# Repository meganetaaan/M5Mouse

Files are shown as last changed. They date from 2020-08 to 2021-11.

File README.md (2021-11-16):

# M5Mouse

A micro mouse PCB module & Software for M5Stack.

## Documents

Assembly and proguramming instructions are documented in the blog series "ししかわのマウス研修（Sskw's micro mouse training）"

- [Japanese](https://rt-net.jp/mobility/archives/9589#toc2)
- [English (auto translate)](https://1-rt--net-jp.translate.goog/mobility/archives/9589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)

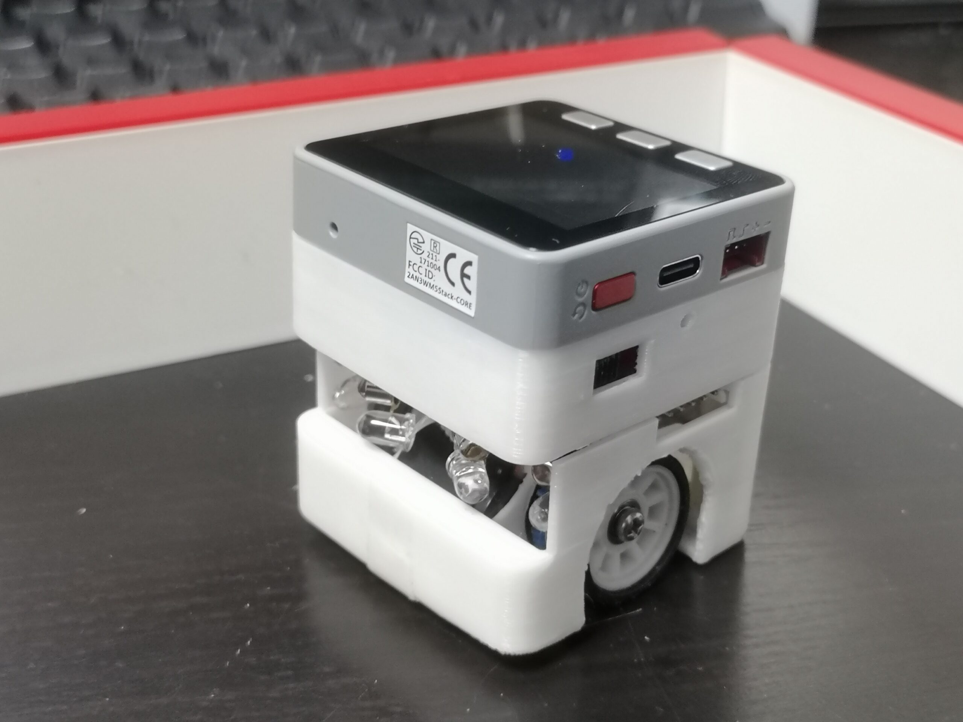
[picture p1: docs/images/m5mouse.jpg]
M5Mouse


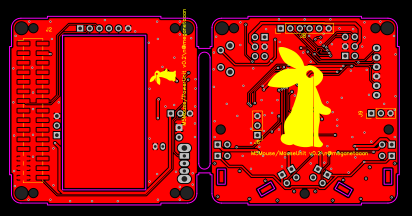
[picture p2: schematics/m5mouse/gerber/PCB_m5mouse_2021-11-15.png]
PCB


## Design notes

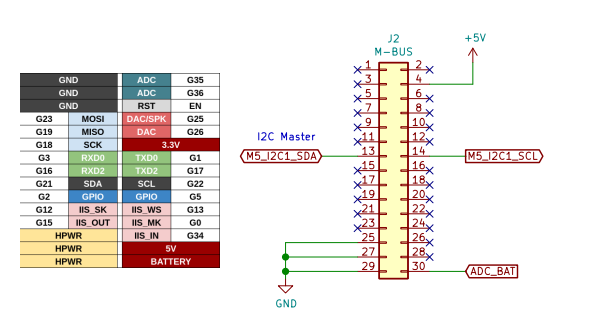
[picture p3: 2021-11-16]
schematics/m5mouse/gerber/M5mouse_pins.png

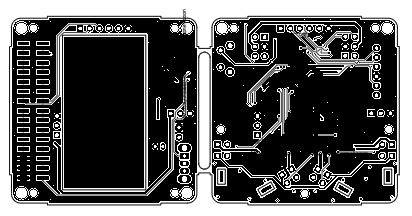
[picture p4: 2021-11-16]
schematics/m5mouse/gerber/PCB_m5mouse_schematic_2021-11-15.png

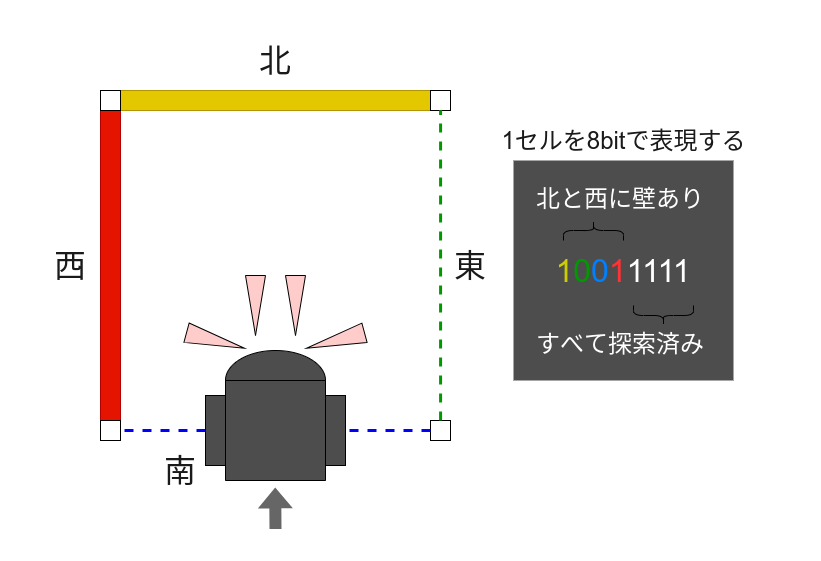
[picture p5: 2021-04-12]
design/cell.drawio.png

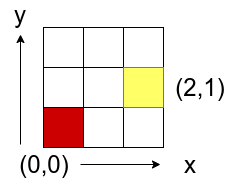
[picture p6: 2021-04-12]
design/maze.drawio.png

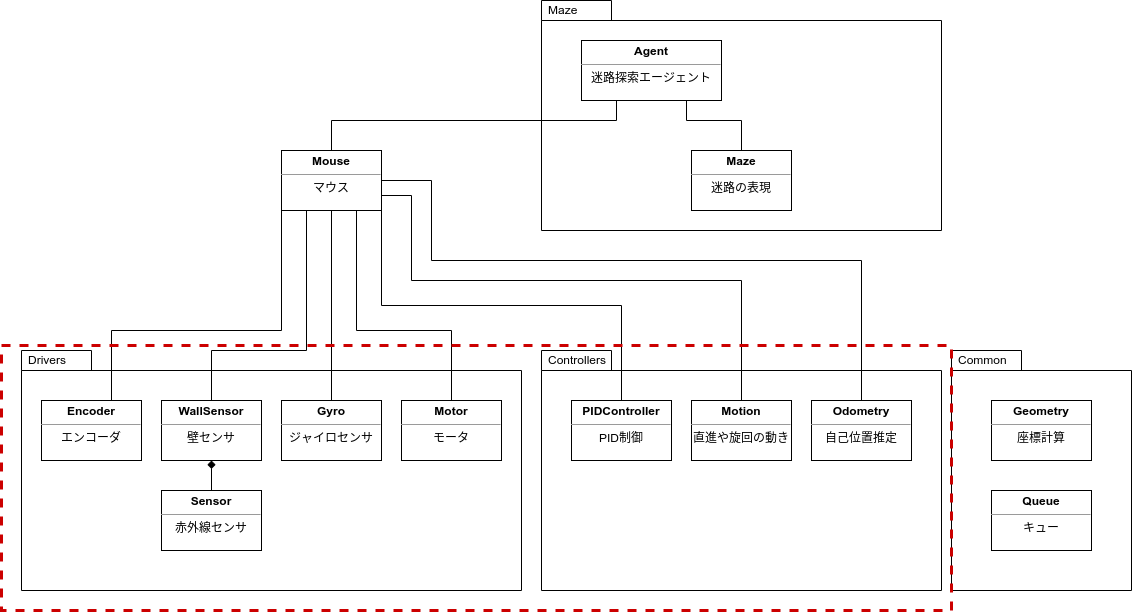
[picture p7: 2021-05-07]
design/class_diagram.drawio.png

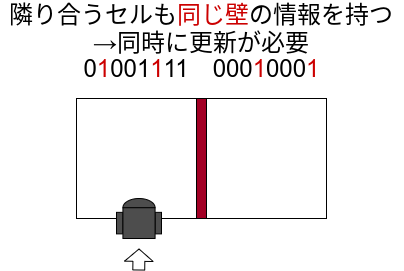
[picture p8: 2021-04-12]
design/neighbor_cells.drawio.png

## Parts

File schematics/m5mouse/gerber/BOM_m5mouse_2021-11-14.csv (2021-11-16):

ID | Name | Designator | Footprint | Quantity | Manufacturer Part | Manufacturer | Supplier | Supplier Part | Price
1 | 0.1u | C3,C4,C11,C12,C13,C14,C16,C20,C21,C22,C29,C30,C31 | C_0402_1005METRIC | 13
2 | 4.7u | C10 | C_0402_1005METRIC | 1
3 | 0.01u | C15 | C_0402_1005METRIC | 1
4 | 1u | C17,C28 | C_0402_1005METRIC | 2
5 | 10u | C18,C19,C25 | C_0402_1005METRIC | 3
6 | 2.2u | C23,C24 | C_0402_1005METRIC | 2
7 | 0.47u | C26 | C_0402_1005METRIC | 1
8 | LED 3.3V | D6,D7 | LED_0603_1608METRIC | 2
9 | LM3940IMP-3.3_NOPB | IC1 | LM3940IMP-3.3NOPB | 1
10 | Conn_02x03_Odd_Even | J4,J5 | PINHEADER_2X03_P2.54MM_VERTICAL | 2
11 | Conn_01x06 | J7 | PINSOCKET_1X06_P2.54MM_VERTICAL | 1
12 | 10u | L1 | L_1008_2520METRIC | 1
13 | BSS138 | Q1,Q3,Q5,Q7 | SOT-23 | 4
14 | 10k | R1,R6,R8,R10,R12,R14,R18 | R_0603_1608METRIC | 7
15 | 5.9k 1% | R2 | R_0603_1608METRIC | 1
16 | 1.07k 1% | R3 | R_0603_1608METRIC | 1
17 | 0 | R4 | R_0603_1608METRIC | 1
18 | 33 | R5 | R_0603_1608METRIC | 1
19 | 1k | R7,R9,R11,R13,R15,R16,R20 | R_0603_1608METRIC | 7
20 | 18k 1% | R17 | R_0603_1608METRIC | 1
21 | 10k 1% | R19 | R_0603_1608METRIC | 1
22 | TPS562200 | U1 | SOT-23-6 | 1
23 | STM32F405RGTx | U2 | LQFP-64_10X10MM_P0.5MM | 1
24 | DRV8835 | U3 | WSON-12-1EP_3X2MM_P0.5MM_EP1X2.65 | 1
25 | 8MHz | Y1 | CSTNE8M00G55Z000R0 | 1
26 | ICM-20648 | U4 | QFN-24-1EP_3X3MM_P0.4MM_EP1.75X1.6MM | 1
27 | SFH4550 | D2,D3,D4,D5 | THROUGHHOLE_1X02_P2.54_VERTICAL | 4
28 | ST-1KL3A | Q2,Q4,Q6,Q8 | THROUGHHOLE_1X02_P2.54_VERTICAL | 4
29 | 10u | C1,C2 | C_0603_1608METRIC | 2
30 | 22u | C5,C6,C7 | C_0805_2012METRIC | 3
31 | 33u | C27 | C_1206_3216METRIC | 1
32 | LED 5V | D1 | LED_D3.0MM_HORIZONTAL_O1.27MM_Z2.0MM | 1
33 | 0 | R21 | R_0603_1608METRIC_PAD1.05X0.95MM_HANDSOLDER | 1
34 | SWD | J3 | JST_EH_S6B-EH_1X06_P2.50MM_HORIZONTAL | 1
35 | 32.768kHz | Y2 | WMRAG32K76CS3C00R0 | 1
36 | 1p | C8,C9 | C_0201_0603METRIC | 2
37 | Ferrite_Bead | FB1 | R_0603_1608METRIC | 1
38 | SW_SPDT | SW1 | SW_CUK_OS102011MA1QN1_SPDT_ANGLED | 1
39 | SW_Push | SW2 | SW_TACTILE_SPST_ANGLED_PTS645VX39-2LFS | 1
40 | Conn_01x02 | J1 | JST_PH_S2B-PH-K_1X02_P2.00MM_HORIZONTAL | 1
41 | Conn_01x03 | J10,J11 | PINSOCKET_1X03_P2.54MM_VERTICAL | 2
42 | LOGO | G | RTMARK_7X7MM | 1
43 | LOGO | G | RT_MARK1_30X30 | 1
44 | MountingHole_2.2mm_M2 | MH10,MH6,MH7 | MOUNTINGHOLE_2.2MM_M2 | 3
45 | mountinghole_M2_M3 | MH8,MH5,MH2,MH3,MH4,MH1 | MOUNTINGHOLE_M2_M3 | 6
46 | M-BUS | J2 | PINHEADER_2X15_P2.54MM_VERTICAL_SMD | 1
47 | Conn_01x06 | J8 | PINHEADER_1X06_P2.54MM_VERTICAL | 1
48 | Conn_01x03 | J6,J9 | PINHEADER_1X03_P2.54MM_VERTICAL | 2

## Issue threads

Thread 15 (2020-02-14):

仮の外装作成

meganetaaan, 2020-02-14:
モータ周辺の外装を作成する。基板は無し。モータを取り付けて動かせればよい。

* [x] 情報収集
  * [x] Faulhaberなど使えそうな3Dモデルを入手する
  * [x] ギヤ・ホイールをFusion360で作る方法を知る
* [x] モータ周りの外装作成
* [x] テストプリント

meganetaaan, 2020-09-30:
作成済み
https://myhub.autodesk360.com/ue29f17411/g/shares/SH919a0QTf3c32634dcf1766a10e55d00c86

Closed 2020-11-20.

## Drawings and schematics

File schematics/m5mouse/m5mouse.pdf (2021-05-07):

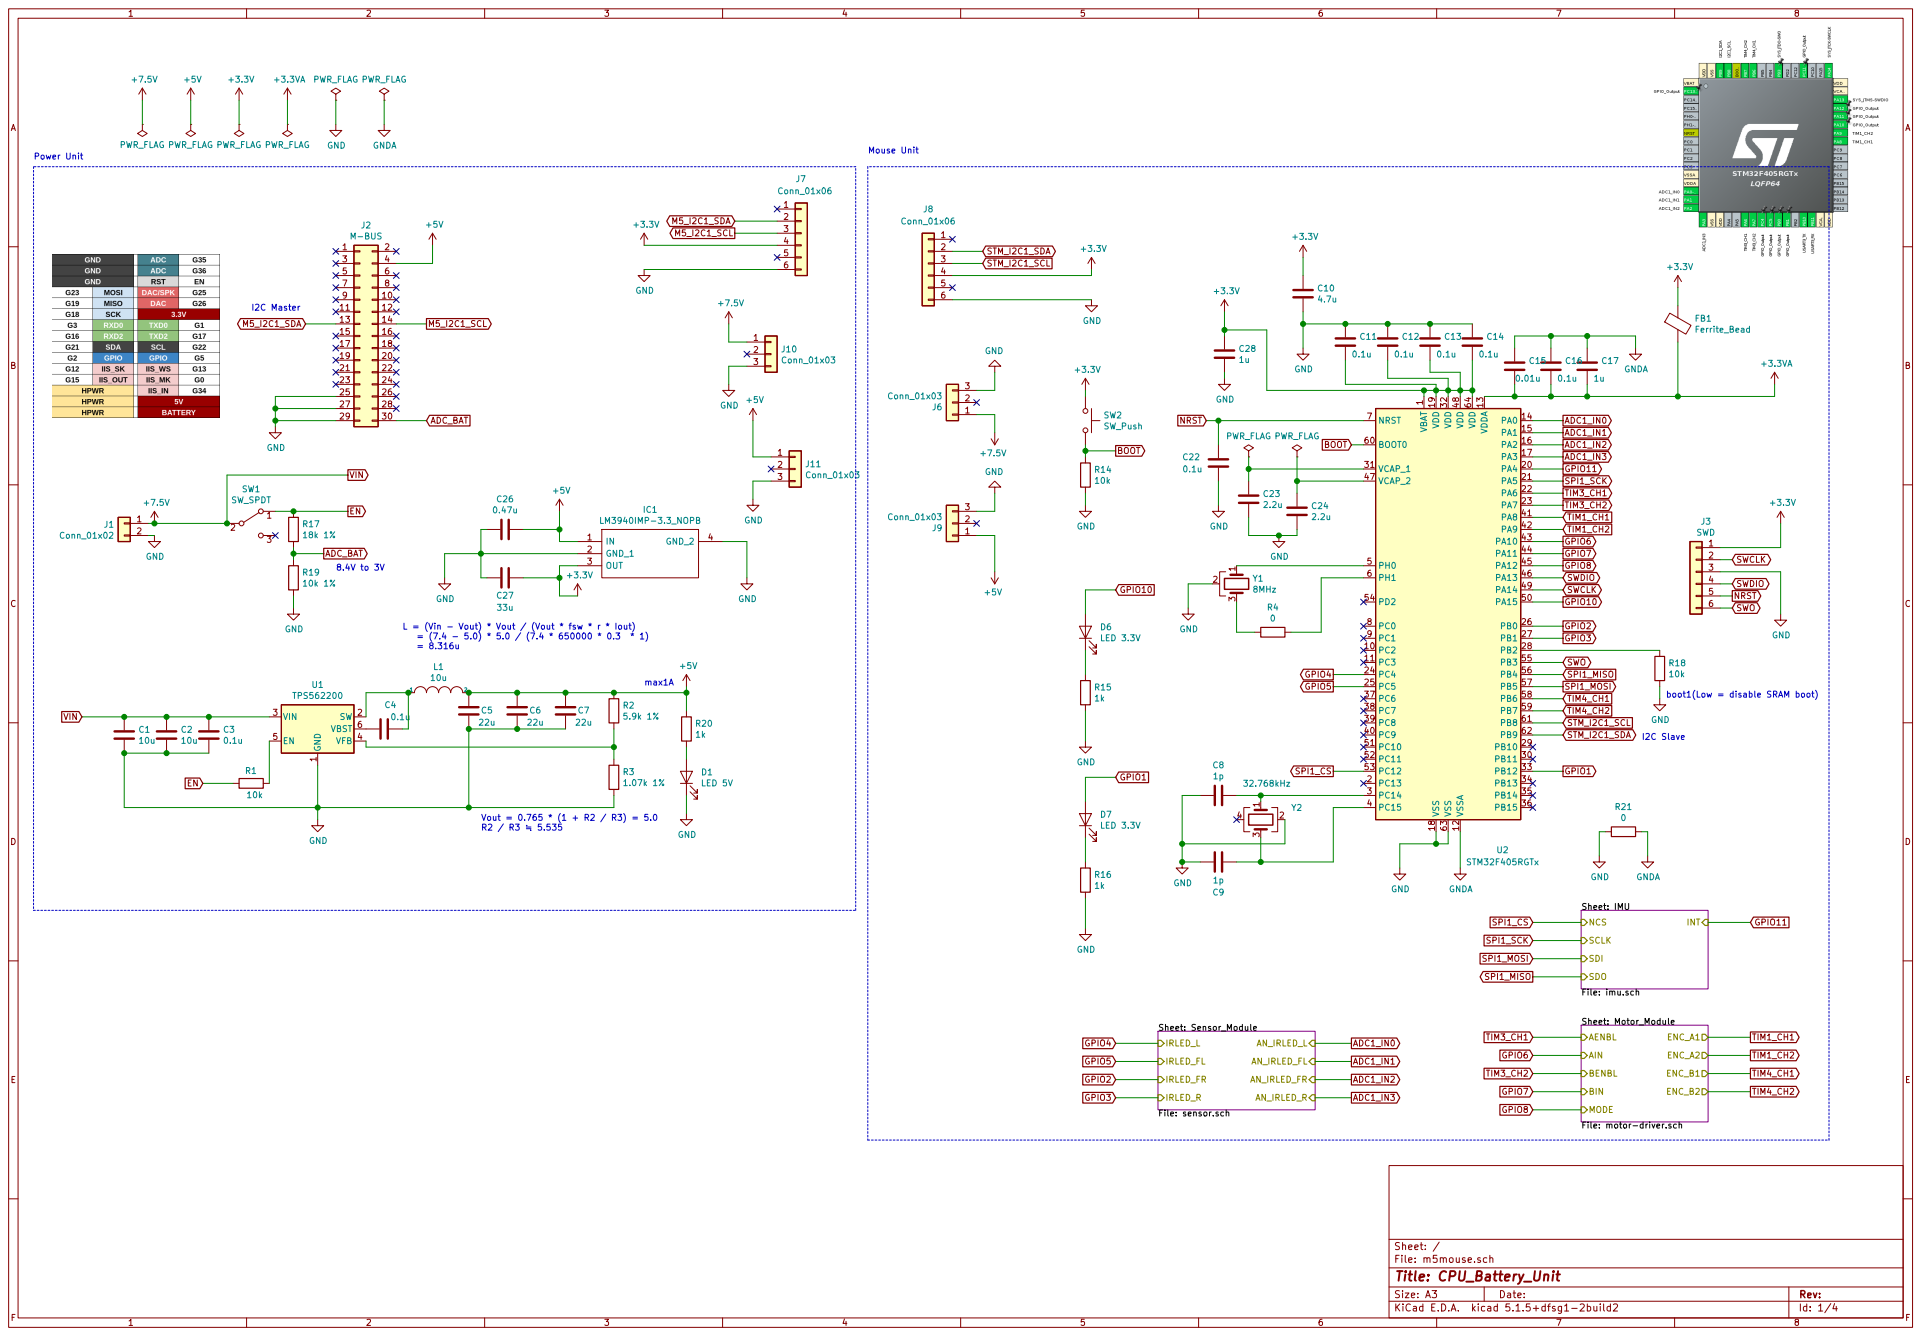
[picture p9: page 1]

1 VCAP_1 31 VCAP_2 47 VDD 19 VDD 32 VDD 48 VDD 64 VDDA 13 VSS 18 VSS 63 VSSA 12 U2 STM32F405RGTx GNDA GND
GPIO6 SPI1_MISO

L = (Vin - Vout) * Vout / (Vout * fsw * r * Iout)

1 SW 2 VIN 3 VFB 4 EN 5 VBST 6 U1 TPS562200

INT Sheet: Motor_Module File: motor-driver.sch AENBL AIN

File: imu.sch SDO

Id: 1/4 Title: CPU_Battery_Unit File: m5mouse.sch Sheet: / Sheet: Sensor_Module File: sensor.sch

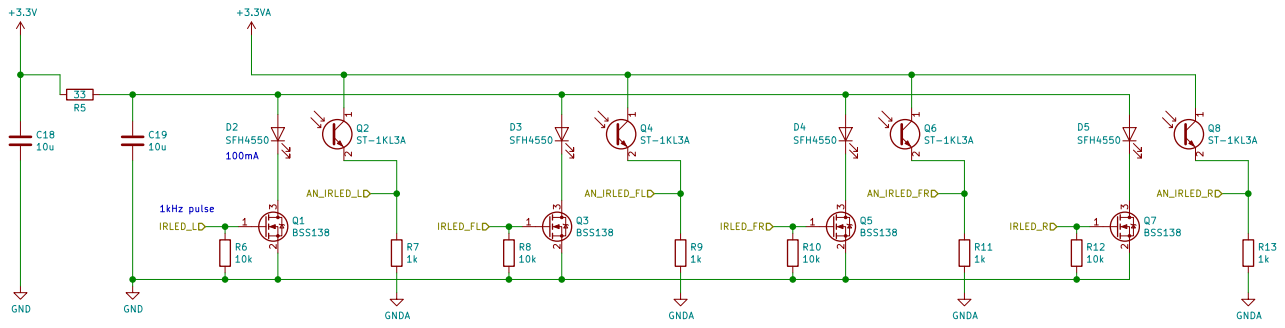
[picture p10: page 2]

1 2 Q2ST-1KL3A D4SFH4550 GNDA GNDA GNDA GNDA

Id: 2/4 Title: File: sensor.sch Sheet: /Sensor_Module/ R6

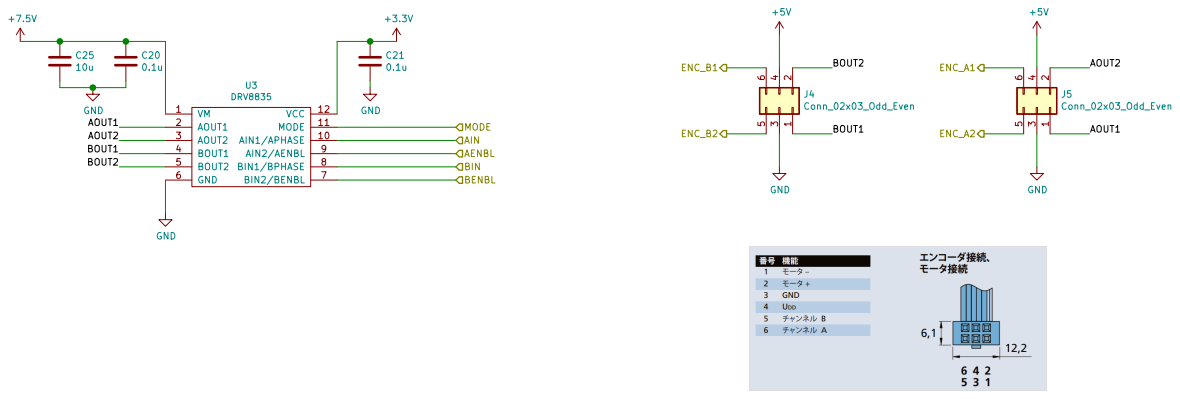
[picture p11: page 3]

Id: 3/4 Title: File: motor-driver.sch Sheet: /Motor_Module/ GND

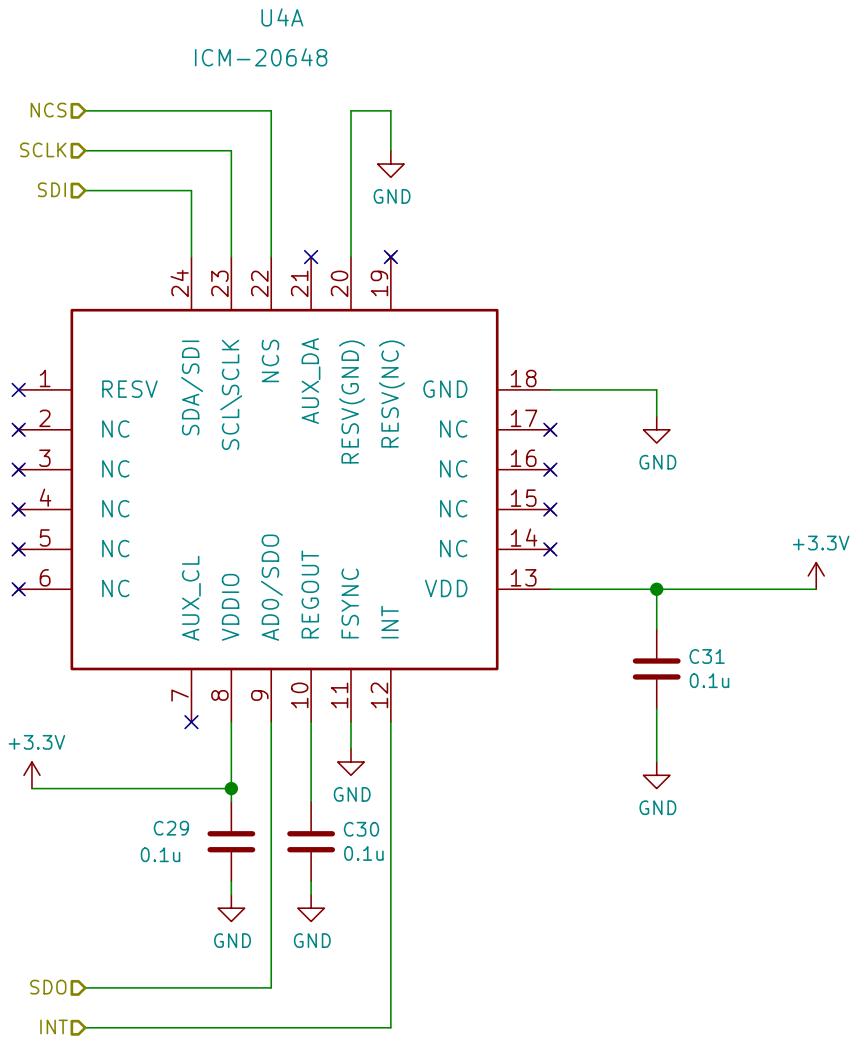
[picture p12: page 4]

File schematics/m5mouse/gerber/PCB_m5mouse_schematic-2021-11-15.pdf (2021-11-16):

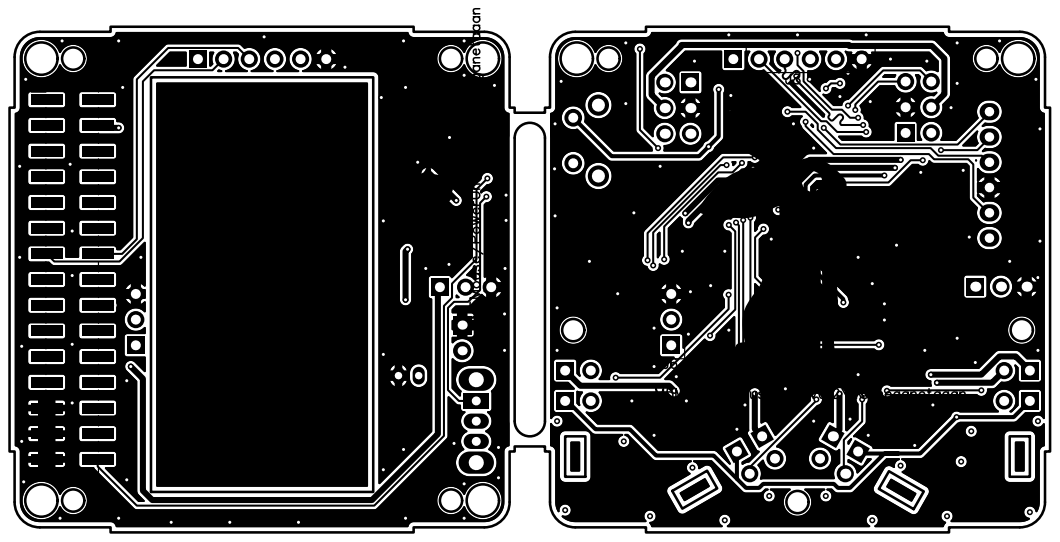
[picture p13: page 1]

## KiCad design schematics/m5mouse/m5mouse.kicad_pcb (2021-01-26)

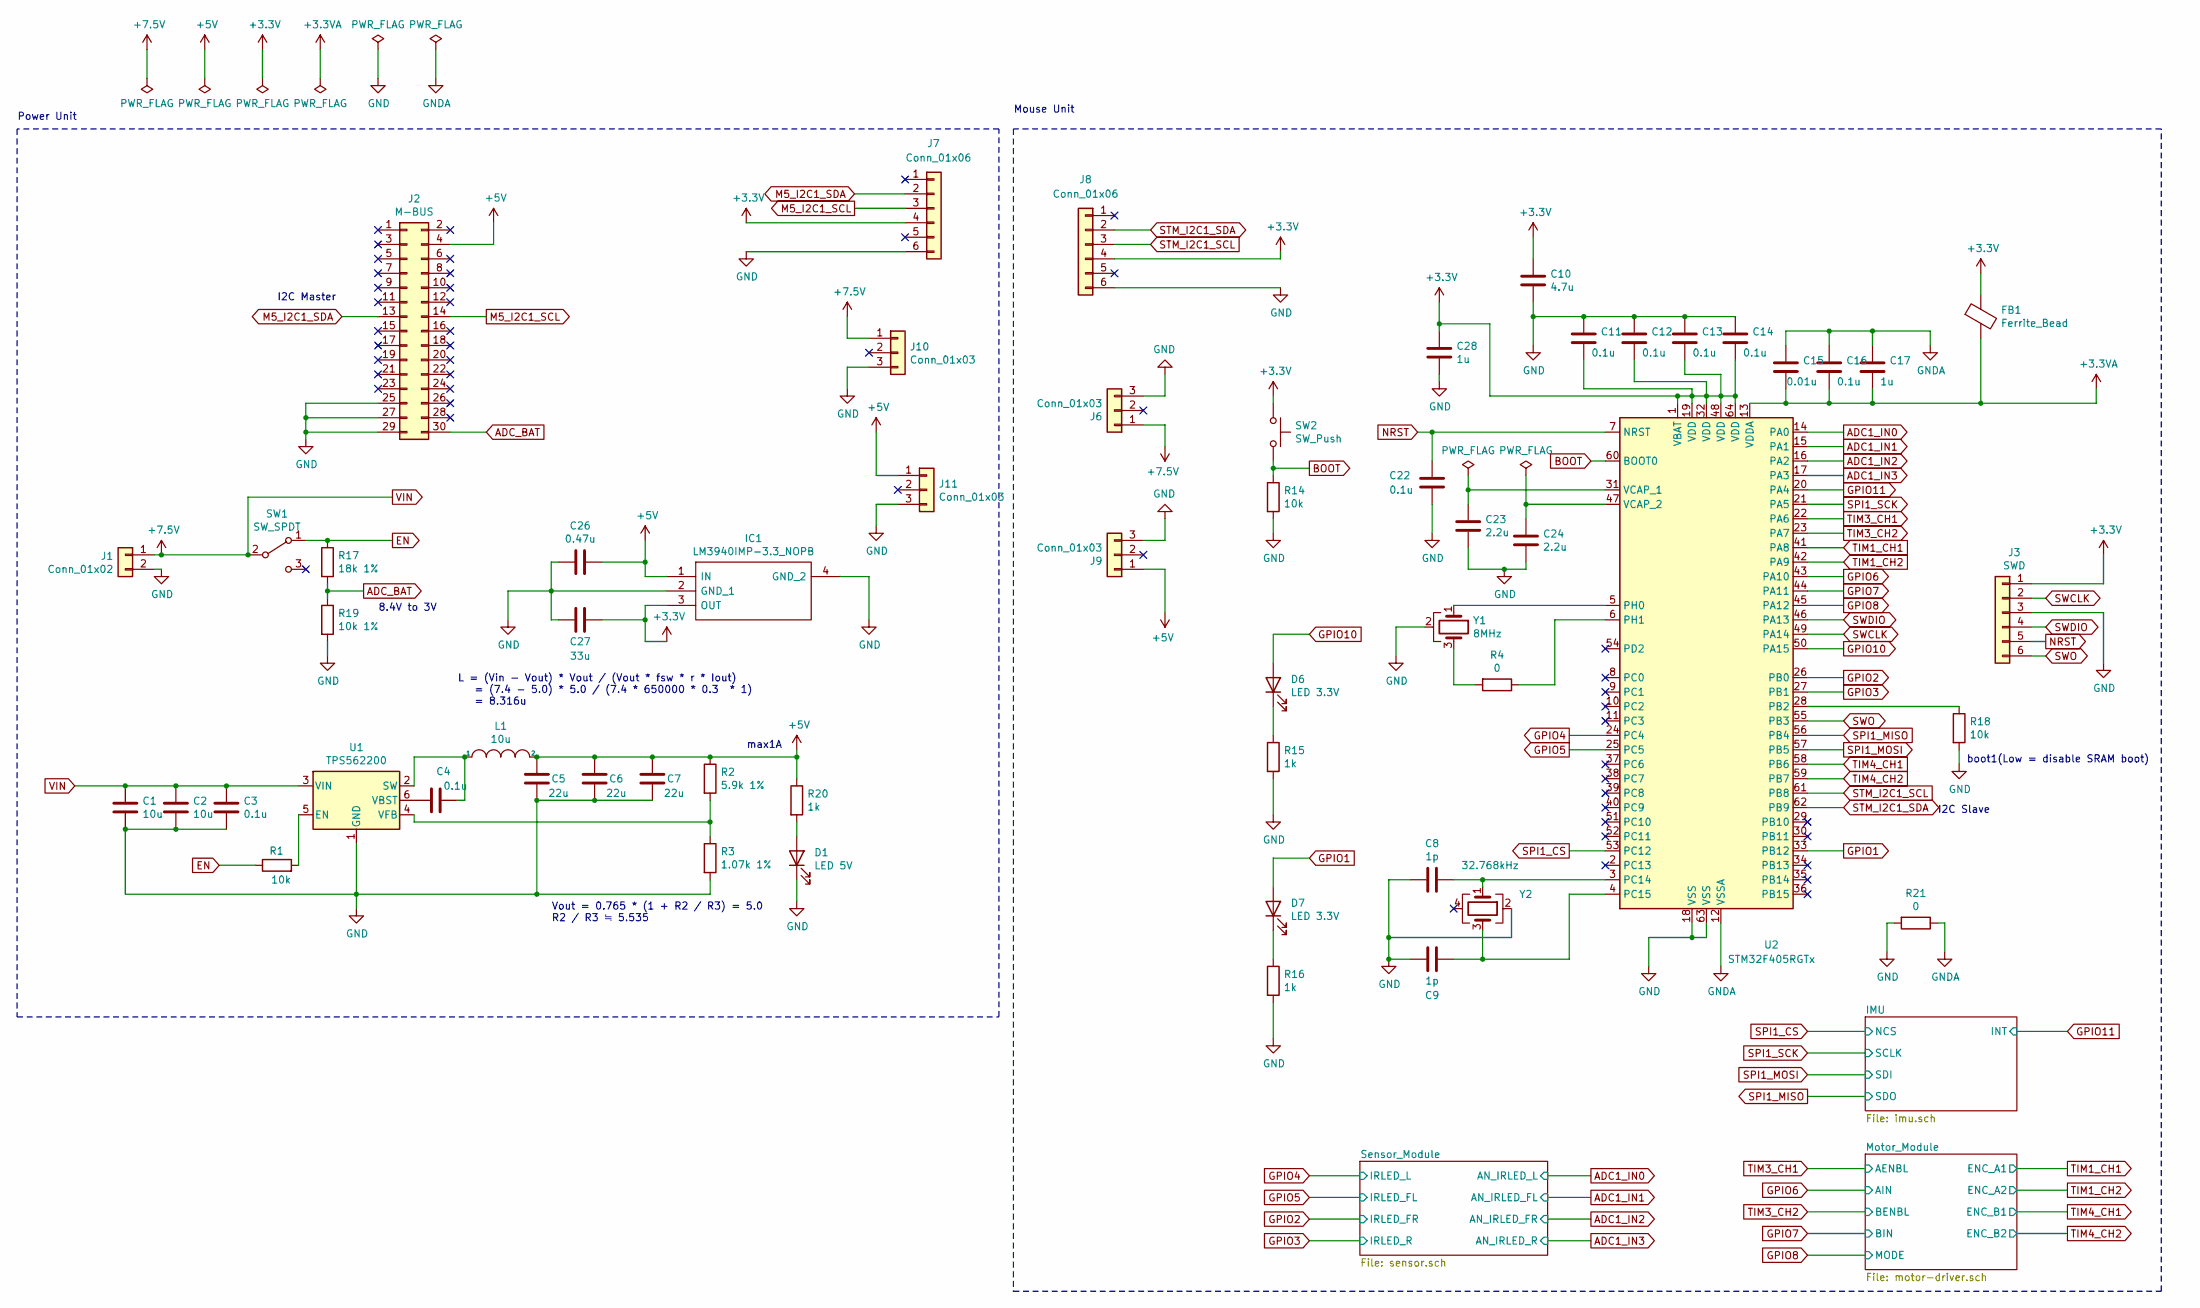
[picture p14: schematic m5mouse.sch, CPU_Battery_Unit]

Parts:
C1, C2: 10u; C_0603_1608Metric
C3, C4, C11, C12, C13, C14, C16, C22: 0.1u; C_0402_1005Metric
C5, C6, C7: 22u; C_0805_2012Metric
C8, C9: 1p; C_0201_0603Metric
C10: 4.7u; C_0402_1005Metric
C15: 0.01u; C_0402_1005Metric
C17, C28: 1u; C_0402_1005Metric
C23, C24: 2.2u; C_0402_1005Metric
C26: 0.47u; C_0402_1005Metric
C27: 33u; C_1206_3216Metric
D1: LED 5V; LED_D3.0mm_Horizontal_O1.27mm_Z2.0mm
D6, D7: LED 3.3V; LED_0603_1608Metric
FB1: Ferrite_Bead; R_0603_1608Metric
IC1: LM3940IMP-3.3_NOPB; LM3940IMP-3.3NOPB; Mouser Part Number 926-LM3940IMP3.3NOPB
J1: Conn_01x02; JST_PH_S2B-PH-K_1x02_P2.00mm_Horizontal
J2: M-BUS; PinHeader_2x15_P2.54mm_Vertical_SMD
J3: SWD; JST_EH_S6B-EH_1x06_P2.50mm_Horizontal
J6, J9: Conn_01x03; PinHeader_1x03_P2.54mm_Vertical
J7: Conn_01x06; PinSocket_1x06_P2.54mm_Vertical
J8: Conn_01x06; PinHeader_1x06_P2.54mm_Vertical
J10, J11: Conn_01x03; PinSocket_1x03_P2.54mm_Vertical
L1: 10u; L_1008_2520Metric
R1, R14, R18: 10k; R_0603_1608Metric
R2: 5.9k 1%; R_0603_1608Metric
R3: 1.07k 1%; R_0603_1608Metric
R4: 0; R_0603_1608Metric
R15, R16, R20: 1k; R_0603_1608Metric
R17: 18k 1%; R_0603_1608Metric
R19: 10k 1%; R_0603_1608Metric
R21: 0; R_0603_1608Metric_Pad1.05x0.95mm_HandSolder
SW1: SW_SPDT; SW_CuK_OS102011MA1QN1_SPDT_Angled
SW2: SW_Push; SW_Tactile_SPST_Angled_PTS645Vx39-2LFS
U1: TPS562200; SOT-23-6
U2: STM32F405RGTx; LQFP-64_10x10mm_P0.5mm
Y1: 8MHz; CSTNE8M00G55Z000R0
Y2: 32.768kHz; WMRAG32K76CS3C00R0

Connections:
+3.3VA: C15.2, C16.2, C17.2, FB1.2, U2.13 (VDDA); also elsewhere on the board
+3V3: C10.1, C11.2, C12.2, C13.2, C14.2, C27.1, C28.1, FB1.1, IC1.3 (OUT), J3.1, J7.4, J8.4, SW2.1, U2.1 (VBAT), U2.19 (VDD), U2.32 (VDD), U2.48 (VDD), U2.64 (VDD); also elsewhere on the board
+5V: C5.2, C6.2, C7.2, C26.1, IC1.1 (IN), J2.4, J9.1, J11.1, L1.2, R2.1, R20.1; also elsewhere on the board
ADC1_IN0: U2.14 (PA0); also elsewhere on the board
ADC1_IN1: U2.15 (PA1); also elsewhere on the board
ADC1_IN2: U2.16 (PA2); also elsewhere on the board
ADC1_IN3: U2.17 (PA3); also elsewhere on the board
ADC_BAT: J2.30, R17.2, R19.1
BOOT: R14.1, SW2.2, U2.60 (BOOT0)
EN: R1.1, R17.1, SW1.1 (A)
GND: C1.2, C2.2, C3.2, C5.1, C6.1, C7.1, C8.2, C9.2, C10.2, C11.1, C12.1, C13.1, C14.1, C22.2, C23.2, C24.2, C26.2, C27.2, C28.2, D1.1 (K), IC1.2 (GND_1), IC1.4 (GND_2), J1.2, J2.25, J2.27, J2.29, J3.3, J6.3, J7.6, J8.6, J9.3, J10.3, J11.3, R3.2, R14.2, R15.2, R16.2, R18.2, R19.2, R21.2, U1.1 (GND), U2.18 (VSS), U2.63 (VSS), Y1.2, Y2.2; also elsewhere on the board
GNDA: C15.1, C16.1, C17.1, R21.1, U2.12 (VSSA); also elsewhere on the board
GPIO1: D7.2 (A), U2.33 (PB12)
GPIO2: U2.26 (PB0); also elsewhere on the board
GPIO3: U2.27 (PB1); also elsewhere on the board
GPIO4: U2.24 (PC4); also elsewhere on the board
GPIO5: U2.25 (PC5); also elsewhere on the board
GPIO6: U2.43 (PA10); also elsewhere on the board
GPIO7: U2.44 (PA11); also elsewhere on the board
GPIO8: U2.45 (PA12); also elsewhere on the board
GPIO10: D6.2 (A), U2.50 (PA15)
GPIO11: U2.20 (PA4); also elsewhere on the board
M5_I2C1_SCL: J2.14, J7.3
M5_I2C1_SDA: J2.13, J7.2
NRST: C22.1, J3.5, U2.7 (NRST)
unnamed: C4.1, L1.1, U1.2 (SW)
unnamed: C4.2, U1.6 (VBST)
unnamed: C8.1, U2.3 (PC14), Y2.1
unnamed: C9.1, U2.4 (PC15), Y2.3
unnamed: C23.1, U2.31 (VCAP_1)
unnamed: C24.1, U2.47 (VCAP_2)
unnamed: D1.2 (A), R20.2
unnamed: D6.1 (K), R15.1
unnamed: D7.1 (K), R16.1
unnamed: R1.2, U1.5 (EN)
unnamed: R2.2, R3.1, U1.4 (VFB)
unnamed: R4.1, U2.6 (PH1)
unnamed: R4.2, Y1.3
unnamed: R18.1, U2.28 (PB2)
unnamed: U2.5 (PH0), Y1.1
SPI1_CS: U2.53 (PC12); also elsewhere on the board
SPI1_MISO: U2.56 (PB4); also elsewhere on the board
SPI1_MOSI: U2.57 (PB5); also elsewhere on the board
SPI1_SCK: U2.21 (PA5); also elsewhere on the board
STM_I2C1_SCL: J8.3, U2.61 (PB8)
STM_I2C1_SDA: J8.2, U2.62 (PB9)
SWCLK: J3.2, U2.49 (PA14)
SWDIO: J3.4, U2.46 (PA13)
SWO: J3.6, U2.55 (PB3)
TIM1_CH1: U2.41 (PA8); also elsewhere on the board
TIM1_CH2: U2.42 (PA9); also elsewhere on the board
TIM3_CH1: U2.22 (PA6); also elsewhere on the board
TIM3_CH2: U2.23 (PA7); also elsewhere on the board
TIM4_CH1: U2.58 (PB6); also elsewhere on the board
TIM4_CH2: U2.59 (PB7); also elsewhere on the board
VIN: C1.1, C2.1, C3.1, J1.1, J6.1, J10.1, SW1.2 (B), U1.3 (VIN); also elsewhere on the board

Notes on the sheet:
I2C Slave
I2C Master
Power Unit
Mouse Unit
L = (Vin - Vout) * Vout / (Vout * fsw * r * Iout) = (7.4 - 5.0) * 5.0 / (7.4 * 650000 * 0.3 * 1) = 8.316u
max1A
boot1(Low = disable SRAM boot)
Vout = 0.765 * (1 + R2 / R3) = 5.0 R2 / R3 ≒ 5.535
8.4V to 3V

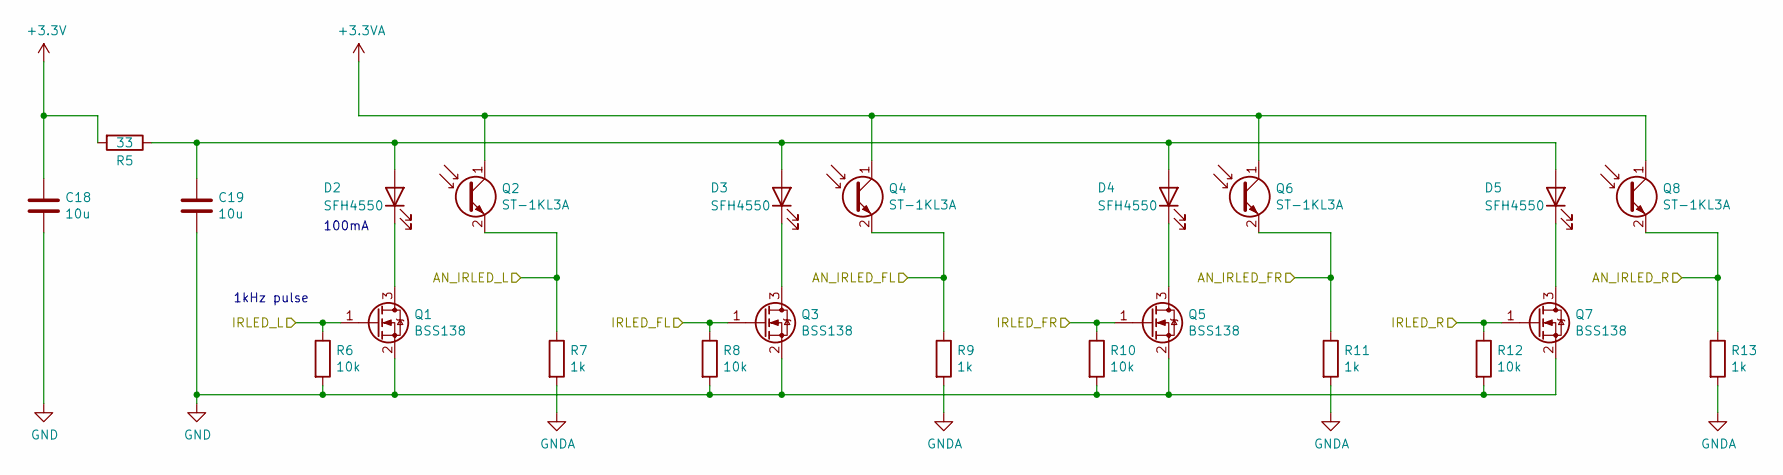
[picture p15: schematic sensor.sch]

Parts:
C18, C19: 10u; C_0402_1005Metric
D2, D3, D4, D5: SFH4550; ThroughHole_1x02_P2.54_Vertical
Q1, Q3, Q5, Q7: BSS138; SOT-23
Q2, Q4, Q6, Q8: ST-1KL3A; ThroughHole_1x02_P2.54_Vertical
R5: 33; R_0603_1608Metric
R6, R8, R10, R12: 10k; R_0603_1608Metric
R7, R9, R11, R13: 1k; R_0603_1608Metric

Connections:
+3.3VA: Q2.1 (C), Q4.1 (C), Q6.1 (C), Q8.1 (C); also elsewhere on the board
+3V3: C18.1, R5.2; also elsewhere on the board
ADC1_IN0: Q2.2 (E), R7.1; also elsewhere on the board
ADC1_IN1: Q4.2 (E), R9.1; also elsewhere on the board
ADC1_IN2: Q6.2 (E), R11.1; also elsewhere on the board
ADC1_IN3: Q8.2 (E), R13.1; also elsewhere on the board
GND: C18.2, C19.2, Q1.2 (S), Q3.2 (S), Q5.2 (S), Q7.2 (S), R6.2, R8.2, R10.2, R12.2; also elsewhere on the board
GNDA: R7.2, R9.2, R11.2, R13.2; also elsewhere on the board
GPIO2: Q5.1 (G), R10.1; also elsewhere on the board
GPIO3: Q7.1 (G), R12.1; also elsewhere on the board
GPIO4: Q1.1 (G), R6.1; also elsewhere on the board
GPIO5: Q3.1 (G), R8.1; also elsewhere on the board
unnamed: C19.1, D2.2 (A), D3.2 (A), D4.2 (A), D5.2 (A), R5.1
unnamed: D2.1 (K), Q1.3 (D)
unnamed: D3.1 (K), Q3.3 (D)
unnamed: D4.1 (K), Q5.3 (D)
unnamed: D5.1 (K), Q7.3 (D)

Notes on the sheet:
1kHz pulse
100mA

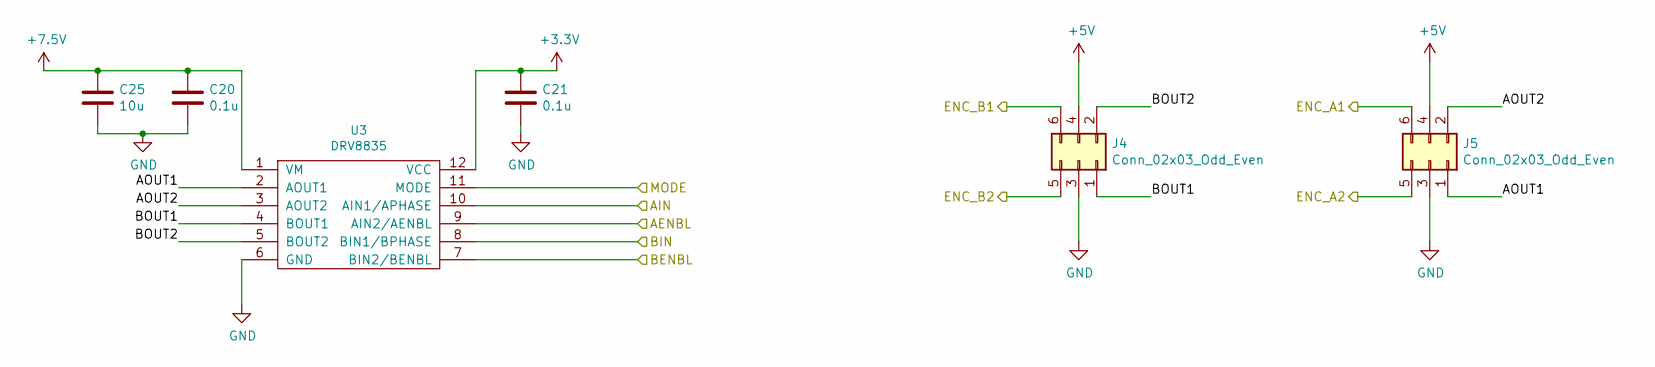
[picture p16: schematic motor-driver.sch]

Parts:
C20, C21: 0.1u; C_0402_1005Metric
C25: 10u; C_0402_1005Metric
J4, J5: Conn_02x03_Odd_Even; PinHeader_2x03_P2.54mm_Vertical
U3: DRV8835; WSON-12-1EP_3x2mm_P0.5mm_EP1x2.65

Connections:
+3V3: C21.1, U3.12 (VCC); also elsewhere on the board
+5V: J4.4, J5.4; also elsewhere on the board
/Motor_Module/AOUT1: J5.1, U3.2 (AOUT1)
/Motor_Module/AOUT2: J5.2, U3.3 (AOUT2)
/Motor_Module/BOUT1: J4.1, U3.4 (BOUT1)
/Motor_Module/BOUT2: J4.2, U3.5 (BOUT2)
GND: C20.2, C21.2, C25.2, J4.3, J5.3, U3.6 (GND), U3.13; also elsewhere on the board
GPIO6: U3.10 (AIN1/APHASE); also elsewhere on the board
GPIO7: U3.8 (BIN1/BPHASE); also elsewhere on the board
GPIO8: U3.11 (MODE); also elsewhere on the board
TIM1_CH1: J5.6; also elsewhere on the board
TIM1_CH2: J5.5; also elsewhere on the board
TIM3_CH1: U3.9 (AIN2/AENBL); also elsewhere on the board
TIM3_CH2: U3.7 (BIN2/BENBL); also elsewhere on the board
TIM4_CH1: J4.6; also elsewhere on the board
TIM4_CH2: J4.5; also elsewhere on the board
VIN: C20.1, C25.1, U3.1 (VM); also elsewhere on the board

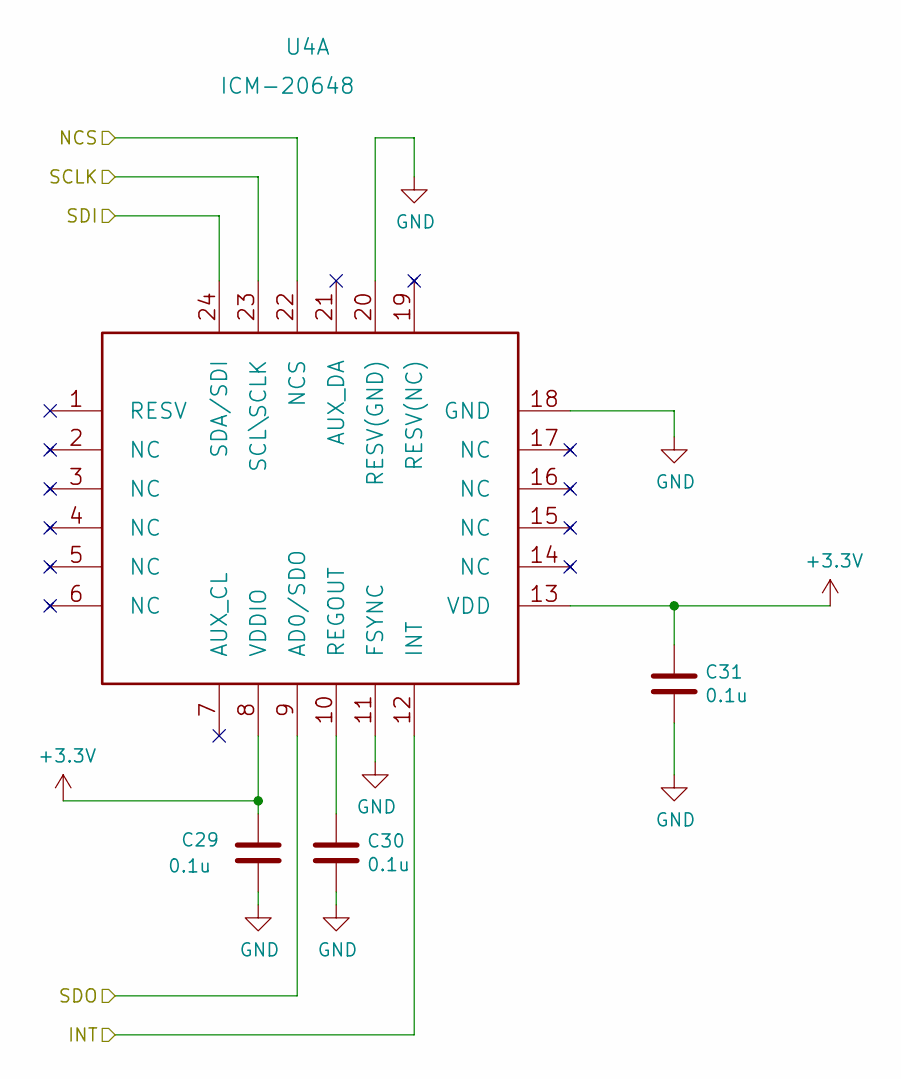
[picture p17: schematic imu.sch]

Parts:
C29, C30, C31: 0.1u; C_0402_1005Metric
U4: ICM-20648; QFN-24-1EP_3x3mm_P0.4mm_EP1.75x1.6mm

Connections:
+3V3: C29.1, C31.1, U4.8 (VDDIO), U4.13 (VDD); also elsewhere on the board
GND: C29.2, C30.2, C31.2, U4.11 (FSYNC), U4.18 (GND), U4.20 (RESV(GND)); also elsewhere on the board
GPIO11: U4.12 (INT); also elsewhere on the board
unnamed: C30.1, U4.10 (REGOUT)
SPI1_CS: U4.22 (NCS); also elsewhere on the board
SPI1_MISO: U4.9 (AD0/SDO); also elsewhere on the board
SPI1_MOSI: U4.24 (SDA/SDI); also elsewhere on the board
SPI1_SCK: U4.23 (SCL\SCLK); also elsewhere on the board

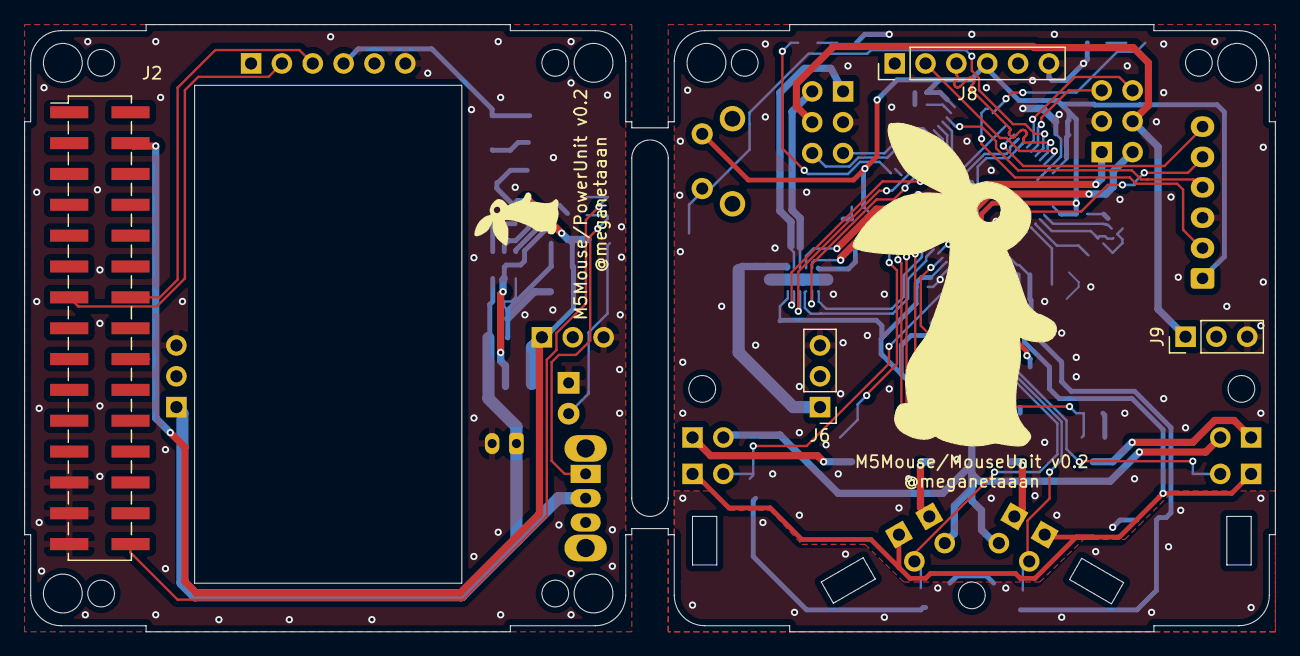
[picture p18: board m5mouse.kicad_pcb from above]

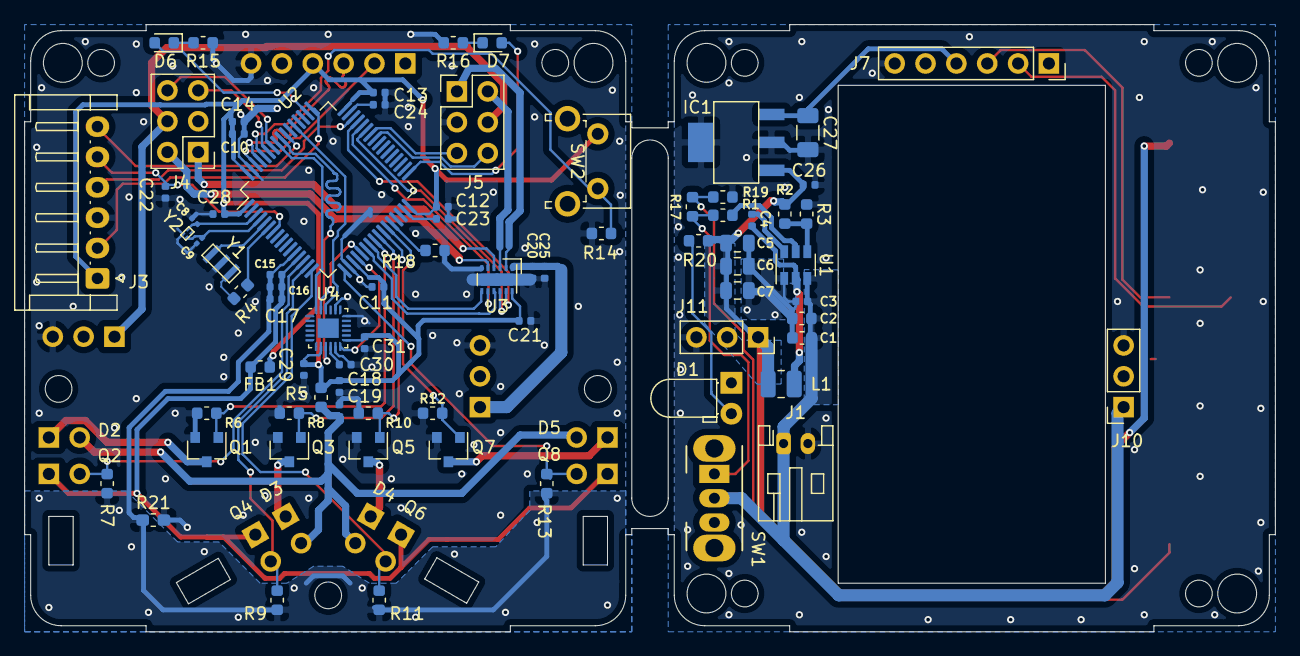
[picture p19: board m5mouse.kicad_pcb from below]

Board: 2 copper layers, 103.0 x 50.0 mm, 98 parts (85 on the bottom side), 66 nets.

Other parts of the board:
MH1, MH2, MH3, MH4, MH5, MH8: mountinghole_M2_M3
MH6, MH7, MH10: MountingHole_2.2mm_M2

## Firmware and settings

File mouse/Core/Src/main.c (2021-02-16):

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

/* Includes ------------------------------------------------------------------*/
#include "main.h"

/* USER CODE BEGIN Includes */
#include <controllers/pid.h>
#include <delay_us.h>
#include <drivers/encoder.h>
#include <drivers/gyro.h>
#include <drivers/motor.h>
#include <drivers/sensor.h>
#include <global.h>
#include <mouse.h>
#include <stdio.h>
#include <stdlib.h>
// #define ARM_MATH_CM4
#include <arm_math.h>
#include "test.h"

#include "controllers/motion.h"
#include "controllers/tracking.h"
#include "maze/agent.h"
#include "maze/maze.h"
#include "maze/maze_data.h"

/* USER CODE END Includes */

ADC_HandleTypeDef hadc1;

I2C_HandleTypeDef hi2c1;

SPI_HandleTypeDef hspi1;

TIM_HandleTypeDef htim1;
TIM_HandleTypeDef htim3;
TIM_HandleTypeDef htim4;
TIM_HandleTypeDef htim6;
TIM_HandleTypeDef htim7;

UART_HandleTypeDef huart3;

void SystemClock_Config(void);
static void MX_GPIO_Init(void);
static void MX_ADC1_Init(void);
static void MX_I2C1_Init(void);
static void MX_TIM1_Init(void);
static void MX_TIM3_Init(void);
static void MX_USART3_UART_Init(void);
static void MX_SPI1_Init(void);
static void MX_TIM4_Init(void);
static void MX_TIM6_Init(void);
static void MX_TIM7_Init(void);
/* USER CODE BEGIN PFP */

extern void initialise_monitor_handles(void);
extern uint32_t m5timerCount;
extern m5Mouse mouse;
extern uint8_t m5transferRequested;
extern uint8_t m5transferDirection;
extern uint8_t m5i2cbuffer[256];

/* USER CODE END PFP */

/**
 * @brief  The application entry point.
 * @retval int
 */
int main(void) {
  /* USER CODE BEGIN 1 */
  // #ifdef DEBUG
  // initialise_monitor_handles();
  // #endif


  /* USER CODE END 1 */

  /* MCU Configuration--------------------------------------------------------*/

  /* Reset of all peripherals, Initializes the Flash interface and the Systick.
   */
  HAL_Init();

  /* Configure the system clock */
  SystemClock_Config();

  /* Initialize all configured peripherals */
  MX_GPIO_Init();
  MX_ADC1_Init();
  MX_I2C1_Init();
  MX_TIM1_Init();
  MX_TIM3_Init();
  MX_USART3_UART_Init();
  MX_SPI1_Init();
  MX_TIM4_Init();
  MX_TIM6_Init();
  MX_TIM7_Init();
  /* USER CODE BEGIN 2 */

  // 開始
  m5main_init_mouse();
  m5mouse_start(mouse);
  // mouse->active = 0;

  // 割り込みハンドラの開始
  HAL_TIM_Base_Start_IT(&htim7);
  HAL_TIM_Base_Start_IT(&htim6);
  m5Maze maze = m5maze_constructor();
  m5MazeAgent agent = m5mazeagent_constructor(maze, mouse);
  HAL_Delay(500);
  // m5mouse_slalom(mouse, 90, mouse->cap_velocity.v, mouse->cap_accel.alpha, mouse->cap_velocity.omega);

/*
  m5Motion straight = m5motion_constructor(M5_STRAIGHT, (m5Velocity){0, 0}, (m5Velocity){400, 0}, (m5Velocity){0, 0}, (m5Position){0, M5_MAZE_WIDTH * 8, 0}, (m5Accel){800, 0}, 1000);
  size_t count = 0;
  m5Odometry odo = m5odometry_constructor(M5_DELTA);
  odo->position = (m5Position){20, 0, 0};
  m5Velocity current_velocity = (m5Velocity){0, 0};
  m5Velocity prev_velocity = (m5Velocity){0, 0};
  m5TrackTarget  target;
  while (!straight->is_end) {
    current_velocity = m5v_add(m5v_mul(current_velocity, 0.9), m5v_mul(prev_velocity, 0.1));
    m5odometry_update(odo, current_velocity);
    target = m5motion_get_next(straight);
    m5Velocity v = m5tracking_get_velocity(odo->position, target);
    m5Position pos = odo->position;
    if (count % 20 == 0) {
      printf("time: %d, odo: (%f, %f, %f), target: (%f, %f, %f)\r\n", count, pos.x, pos.y, pos.theta, target.position.x, target.position.y, target.position.theta);
    }
    prev_velocity = v;
    count++;
  }
  m5Position pos = odo->position;
  printf("time: %d, odo: (%f, %f, %f), target: (%f, %f, %f)\r\n", count, pos.x, pos.y, pos.theta, target.position.x, target.position.y, target.position.theta);
  while (1) {
    // hoge
  }

*/
  /* USER CODE END 2 */

  /* Infinite loop */
  /* USER CODE BEGIN WHILE */
  while (1)

  {
    // printf("transfer complete. count: %d\n", count);
    HAL_StatusTypeDef status =
        HAL_I2C_Slave_Receive(&hi2c1, m5i2cbuffer, 1, 200);
    if (status == HAL_OK) {
      switch (m5i2cbuffer[0]) {
        case M5_REGISTER_WHO_AM_I:
          m5i2cbuffer[0] = M5_VALUE_WHO_AM_I;
          HAL_I2C_Slave_Transmit(&hi2c1, m5i2cbuffer, 1, 100);
          break;
        case M5_REGISTER_RUN_SEARCH:
          mouse->cap_velocity = (m5Velocity){M5_VELOCITY_SEARCH, M5_ANG_VELOCITY};
          HAL_Delay(500);
          m5agent_search_run(agent, (m5Index){7, 8});
          break;
        case M5_REGISTER_RUN_FAST:
          // TODO
          // mouse->cap_velocity = (m5Velocity){M5_VELOCITY, M5_ANG_VELOCITY};
          // m5agent_fast_run(agent, (m5Index){7, 8});
          break;
        case M5_REGISTER_TEST_STRAIGHT:
          m5i2cbuffer[0] = m5i2c_count++;
          m5test_straight(mouse);
          HAL_Delay(300);
          break;
        case M5_REGISTER_TEST_SPIN:
          m5i2cbuffer[0] = m5i2c_count++;
          m5test_spin(mouse);
          HAL_Delay(300);
          break;
        case M5_REGISTER_TEST_SLALOM:
          m5i2cbuffer[0] = m5i2c_count++;
          m5test_slalom(mouse);
          HAL_Delay(300);
          break;
        case M5_REGISTER_TEST_ZIG_ZAG:
          m5i2cbuffer[0] = m5i2c_count++;
          m5test_zig_zag(mouse);
          HAL_Delay(300);
          break;
        case M5_REGISTER_TEST_CRANK:
          m5i2cbuffer[0] = m5i2c_count++;
          m5test_crank(mouse);
          HAL_Delay(300);
          break;
        case M5_REGISTER_RESET:
          m5i2cbuffer[0] = m5i2c_count++;
          m5odometry_reset(mouse->odometry);
          HAL_Delay(300);
          break;
        case M5_REGISTER_CALIBRATE:
          HAL_Delay(500);
          m5test_calibrate(mouse);
          HAL_Delay(500);
          m5test_calibrate_wall(mouse);
          mouse->is_wall_adjust_enabled = 1;
          break;
        default:
          m5i2cbuffer[0] = 0xFF;
      }
      while (HAL_I2C_GetState(&hi2c1) != HAL_I2C_STATE_READY)
        ;
    } else {
      // printf("error %d\n", status);
    }
    /* USER CODE END WHILE */

    /* USER CODE BEGIN 3 */
  }
  /* USER CODE END 3 */
}

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
/* USER CODE BEGIN 4 */
void m5main_init_mouse(void) {
  // DRV8835のモード指定（PHASE/ENBLモード）
  HAL_GPIO_WritePin(GPIOA, GPIO_PIN_12, GPIO_PIN_SET);

  // モータ初期化
  m5TimerConfiguration timerMotorL = malloc(sizeof(m5TimerConfigurationRecord));
  timerMotorL->handler = &htim3;
  timerMotorL->channel = TIM_CHANNEL_1;
  m5Motor motorL = malloc(sizeof(m5MotorRecord));
  motorL->dir_port = GPIOA;
  motorL->dir_pin = GPIO_PIN_10;
  motorL->direction = 0;
  motorL->timer = timerMotorL;
  m5motor_init(motorL);
  mouse->motor_l = motorL;

  m5TimerConfiguration timerMotorR = malloc(sizeof(m5TimerConfigurationRecord));
  timerMotorR->handler = &htim3;
  timerMotorR->channel = TIM_CHANNEL_2;
  m5Motor motorR = malloc(sizeof(m5MotorRecord));
  motorR->dir_port = GPIOA;
  motorR->dir_pin = GPIO_PIN_11;
  motorR->direction = 1;
  motorR->timer = timerMotorR;
  m5motor_init(motorR);
  mouse->motor_r = motorR;

  // IMUの初期化
  HAL_Delay(50);
  m5SPIConfiguration spi = malloc(sizeof(m5SPIConfigurationRecord));
  spi->cs_pin = GPIO_PIN_12;
  spi->cs_port = GPIOC;
  spi->handler = &hspi1;
  m5Gyro gyro = malloc(sizeof(m5GyroRecord));
  gyro->spi = spi;
  m5gyro_init(gyro);
  mouse->gyro = gyro;

  // エンコーダの初期化
  m5Encoder encoderL = malloc(sizeof(m5EncoderRecord));
  m5Encoder encoderR = malloc(sizeof(m5EncoderRecord));
  m5TimerConfiguration timerL = malloc(sizeof(m5TimerConfigurationRecord));
  m5TimerConfiguration timerR = malloc(sizeof(m5TimerConfigurationRecord));
  timerL->handler = &htim1;
  encoderL->timer = timerL;
  encoderL->direction = 1;
  m5encoder_init(encoderL);
  mouse->encoder_l = encoderL;
  timerR->handler = &htim4;
  encoderR->timer = timerR;
  encoderR->direction = 0;
  m5encoder_init(encoderR);
  mouse->encoder_r = encoderR;

  m5AnalogConfiguration adRec_l = malloc(sizeof(m5AnalogConfigurationRecord));
  adRec_l->handler = &hadc1;
  adRec_l->channel = (ADC_ChannelConfTypeDef *)ADC_CHANNEL_1;
  m5Sensor sensor_l = malloc(sizeof(m5SensorRecord));
  sensor_l->analog = adRec_l;
  sensor_l->led_port = GPIOC;
  sensor_l->led_pin = GPIO_PIN_5;
  m5sensor_init(sensor_l);

  m5AnalogConfiguration adRec_fl = malloc(sizeof(m5AnalogConfigurationRecord));
  adRec_fl->handler = &hadc1;
  adRec_fl->channel = (ADC_ChannelConfTypeDef *)ADC_CHANNEL_0;
  m5Sensor sensor_fl = malloc(sizeof(m5SensorRecord));
  sensor_fl->analog = adRec_fl;
  sensor_fl->led_port = GPIOC;
  sensor_fl->led_pin = GPIO_PIN_4;
  m5sensor_init(sensor_fl);

  m5AnalogConfiguration adRec_fr = malloc(sizeof(m5AnalogConfigurationRecord));
  adRec_fr->handler = &hadc1;
  adRec_fr->channel = (ADC_ChannelConfTypeDef *)ADC_CHANNEL_3;
  m5Sensor sensor_fr = malloc(sizeof(m5SensorRecord));
  sensor_fr->analog = adRec_fr;
  sensor_fr->led_port = GPIOB;
  sensor_fr->led_pin = GPIO_PIN_1;
  m5sensor_init(sensor_fr);

  m5AnalogConfiguration adRec_r = malloc(sizeof(m5AnalogConfigurationRecord));
  adRec_r->handler = &hadc1;
  adRec_r->channel = (ADC_ChannelConfTypeDef *)ADC_CHANNEL_2;
  m5Sensor sensor_r = malloc(sizeof(m5SensorRecord));
  sensor_r->analog = adRec_r;
  sensor_r->led_port = GPIOB;
  sensor_r->led_pin = GPIO_PIN_0;
  m5sensor_init(sensor_r);

  m5WallSensor ws =
      m5wallsensor_constructor(sensor_l, sensor_fl, sensor_fr, sensor_r);
  mouse->sensor = ws;

  m5PIDController controller_l =
      m5pid_constructor(M5DEFAULT_PGAIN, M5DEFAULT_IGAIN, M5DEFAULT_DGAIN, M5DEFAULT_SATURATION);
  m5PIDController controller_r =
      m5pid_constructor(M5DEFAULT_PGAIN, M5DEFAULT_IGAIN, M5DEFAULT_DGAIN, M5DEFAULT_SATURATION);
  m5PIDController controller_wall = m5pid_constructor(
      M5DEFAULT_WALL_PGAIN, M5DEFAULT_WALL_IGAIN, M5DEFAULT_WALL_DGAIN, 10);
  mouse->controller_l = controller_l;
  mouse->controller_r = controller_r;
  mouse->controller_wall = controller_wall;
  mouse->motion_queue = m5queue_constructor();

  mouse->current_velocity = (m5Velocity){0, 0};
  mouse->target_velocity = (m5Velocity){0, 0};
  mouse->cap_velocity = (m5Velocity){M5_VELOCITY_SEARCH, M5_ANG_VELOCITY};
  mouse->cap_accel = (m5Accel){M5_ACCEL_SEARCH, M5_ANG_ACCEL};
  mouse->is_wall_adjust_enabled = 1;
  mouse->odometry = m5odometry_constructor(M5_DELTA);
}

/* USER CODE END 4 */
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


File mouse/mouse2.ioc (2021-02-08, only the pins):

Mcu.UserName=STM32F405RGTx
PA0-WKUP.Signal=ADCx_IN0
PA1.Signal=ADCx_IN1
PA10.Signal=GPIO_Output
PA11.Signal=GPIO_Output
PA12.Signal=GPIO_Output
PA13.Signal=SYS_JTMS-SWDIO
PA14.Signal=SYS_JTCK-SWCLK
PA15.Signal=GPIO_Output
PA2.Signal=ADCx_IN2
PA3.Signal=ADCx_IN3
PA4.Signal=GPIO_Input
PA5.Signal=SPI1_SCK
PA6.Signal=S_TIM3_CH1
PA7.Signal=S_TIM3_CH2
PA8.Signal=S_TIM1_CH1
PA9.Signal=S_TIM1_CH2
PB0.Signal=GPIO_Output
PB1.Signal=GPIO_Output
PB10.Signal=USART3_TX
PB11.Signal=USART3_RX
PB12.Signal=GPIO_Output
PB3.Signal=SYS_JTDO-SWO
PB4.Signal=SPI1_MISO
PB5.Signal=SPI1_MOSI
PB6.Signal=S_TIM4_CH1
PB7.Signal=S_TIM4_CH2
PB8.Signal=I2C1_SCL
PB9.Signal=I2C1_SDA
PC12.Signal=GPIO_Output
PC14-OSC32_IN.Signal=RCC_OSC32_IN
PC15-OSC32_OUT.Signal=RCC_OSC32_OUT
PC4.Signal=GPIO_Output
PC5.Signal=GPIO_Output
PH0-OSC_IN.Signal=RCC_OSC_IN
PH1-OSC_OUT.Signal=RCC_OSC_OUT

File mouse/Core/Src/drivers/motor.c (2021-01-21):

#include "drivers/motor.h"

#include <stdio.h>

void m5motor_init(m5Motor motor) {
  // TODO: initialization
  motor->active = 0;
  motor->duty = 0;
}

void m5motor_start(m5Motor motor) {
  // TODO: Error handler
  HAL_TIM_PWM_Start(motor->timer->handler, motor->timer->channel);
  motor->active = 1;
}

void m5motor_stop(m5Motor motor) {
  // TODO: Error handler
  HAL_TIM_PWM_Stop(motor->timer->handler, motor->timer->channel);
  motor->active = 0;
}

void m5motor_set_voltage(m5Motor motor, float voltage, float battery_voltage) {
  uint8_t direction = 1;
  if (voltage < 0) {
    voltage = -voltage;
    direction = 0;
  }
  uint16_t pwm = voltage * 1000 / battery_voltage;
  m5motor_set_pwm(motor, direction, pwm);
}

void m5motor_set_pwm(m5Motor motor, uint8_t direction, uint16_t pwm) {
  GPIO_PinState state = (motor->direction ^ direction) ? GPIO_PIN_SET : GPIO_PIN_RESET;
  HAL_GPIO_WritePin(motor->dir_port, motor->dir_pin, state);

  __HAL_TIM_SET_COMPARE(motor->timer->handler, motor->timer->channel, pwm);
  // TIM_OC_InitTypeDef sConfigOC = {0};
  // sConfigOC.OCMode = TIM_OCMODE_PWM1;
  // sConfigOC.Pulse = pwm;
  // sConfigOC.OCPolarity = TIM_OCPOLARITY_HIGH;
  // sConfigOC.OCFastMode = TIM_OCFAST_DISABLE;
  // if (HAL_TIM_PWM_ConfigChannel(motor->timer->handler, &sConfigOC, motor->timer->channel) != HAL_OK) {
  //   return;
  // }
  motor->duty = pwm;

  /*
    // TODO: HALの内部関数を使わない方式に差し替え
    TIM_OC_InitTypeDef sConfigOC = {0};
    sConfigOC.OCMode = TIM_OCMODE_PWM1;
    sConfigOC.Pulse = 0;
    sConfigOC.OCPolarity = TIM_OCPOLARITY_HIGH;
    sConfigOC.OCFastMode = TIM_OCFAST_DISABLE;
    if (HAL_TIM_PWM_ConfigChannel(&htim3, &sConfigOC, TIM_CHANNEL_1) != HAL_OK)
    { return;
    }
    if (HAL_TIM_PWM_ConfigChannel(&htim3, &sConfigOC, TIM_CHANNEL_2) != HAL_OK)
    { return;
    }
    }
  */
}

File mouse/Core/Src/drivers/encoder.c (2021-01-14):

#include "drivers/encoder.h"

int16_t m5encoder_get_value(TIM_HandleTypeDef *htim) {
  uint16_t enc_buff = htim->Instance->CNT;
  return enc_buff;
}

void m5encoder_reset_value(TIM_HandleTypeDef *htim) { htim->Instance->CNT = 0; }

int16_t m5encoder_count_encoder(TIM_HandleTypeDef *htim) {
  int16_t count = m5encoder_get_value(htim);
  m5encoder_reset_value(htim);
  return count;
}

void m5encoder_init(m5Encoder encoder) {
  // TODO: MX_TIM1_Initを参考にタイマーの初期化処理を行う
}

void m5encoder_start(m5Encoder encoder) {
  HAL_TIM_Encoder_Start(encoder->timer->handler, TIM_CHANNEL_ALL);
  encoder->active = 1;
}

void m5encoder_stop(m5Encoder encoder) {
  HAL_TIM_Encoder_Stop(encoder->timer->handler, TIM_CHANNEL_ALL);
  encoder->active = 0;
}

int16_t m5encoder_count(m5Encoder encoder) {
  int sign = encoder->direction ? 1 : -1;
  return m5encoder_count_encoder(encoder->timer->handler) * sign;
}

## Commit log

2020-02-14 Add I2C function
2020-02-26 Add PWM
2020-02-26 Add who-am-i communication via I2C
2020-03-27 Fix Timer period
2020-06-19 WIP: Add schematics
    [cpu.sch, m5mouse.kicad_pcb, m5mouse.sch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]
2020-07-03 Add schematics
    [m5mouse.sch, motor-driver.sch, motor.sch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]
2020-07-06 schematic v0.1
    [m5mouse.sch]
2020-07-06 Add schematic image
2020-07-22 Fix schematics
    [m5mouse.sch, motor-driver.sch, sensor.sch]
2020-08-26 Put parts
    [imu.sch, m5mouse.kicad_pcb, m5mouse.sch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]
2020-08-27 Adjust parts positions
    [m5mouse.kicad_pcb, m5mouse.sch, sensor.sch]
2020-08-27 Draw pattern
    [m5mouse.kicad_pcb, m5mouse.sch, sensor.sch]
2020-08-27 Fix path
    [m5mouse.kicad_pcb]
2020-09-01 Connect GNDA and GND via ferrite bead
    [m5mouse.kicad_pcb, m5mouse.sch]
2020-09-01 Add gerber
    [m5mouse-B_Cu.gbr, m5mouse-B_Mask.gbr, m5mouse-B_Paste.gbr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]
2020-09-02 Fix silk overlap
    [m5mouse.kicad_pcb]
2020-09-08 Fix global label direction
    [m5mouse.sch]
2020-09-08 Fix path length
    [m5mouse.kicad_pcb]
2020-09-09 Refactor pattern layout
    [m5mouse.kicad_pcb]
2020-09-09 Fix patterns
    [m5mouse.kicad_pcb]
2020-09-09 Fix pattern
    [m5mouse.kicad_pcb]
2020-09-10 Fix part position and path
    [m5mouse.kicad_pcb]
2020-09-10 Update gerber files
    [m5mouse-B_Cu.gbr, m5mouse-B_Mask.gbr, m5mouse-B_Paste.gbr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]
2020-09-18 Fix schematics and patterns
    [imu.sch, m5mouse.kicad_pcb, m5mouse.sch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]
2020-09-24 Update m5mouse.kicad_pcb
    Fix parts position
    [m5mouse.kicad_pcb]
2020-09-24 Fix parts position
    [m5mouse.kicad_pcb]
2020-09-24 Change ferrite bead
    [m5mouse.kicad_pcb, m5mouse.sch]
2020-09-24 Generate gerber
    [m5mouse-B_Cu.gbr, m5mouse-B_Mask.gbr, m5mouse-B_Paste.gbr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]
2020-09-29 Fix flipped pin header
    [m5mouse.kicad_pcb, m5mouse.sch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]
2020-11-20 generate gerber files archive in script
2021-01-05 carriage return
2021-01-05 Test adc
2021-01-14 Add drivers
2021-01-15 Add sensor driver
2021-01-18 Add pins/i2c
2021-01-18 Add pid update
2021-01-19 WIP: Add i2c
2021-01-19 WIP: set hispeed I2C
2021-01-28 Fix connector
    [m5mouse.sch]
2021-01-28 blink led on hard fault
2021-02-02 Add sensors
2021-02-03 Add calibrate command
2021-02-04 WIP: Add odometry
2021-02-10 WIP: Adjust gain
    [m5mouse.GBL, m5mouse.GBO, m5mouse.GBS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]
2021-11-14 added BOM
    [BOM_m5mouse_2021-11-14.csv]
2021-11-14 Added pick & place
    Generated from easyeda
    [PickAndPlace_m5mouse_2021-11-14.csv]
2021-11-15 Added image and PDF of PCB
2021-11-15 Added PCB image

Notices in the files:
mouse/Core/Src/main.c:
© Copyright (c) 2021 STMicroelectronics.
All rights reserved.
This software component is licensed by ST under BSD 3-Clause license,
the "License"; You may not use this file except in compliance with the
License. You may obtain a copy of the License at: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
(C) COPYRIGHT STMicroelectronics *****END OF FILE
